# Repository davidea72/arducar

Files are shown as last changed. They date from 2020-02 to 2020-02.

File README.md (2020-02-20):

# arducar
arduino based car with mpu 6050 gyro

l' intento è quello di realizzare una macchinina comandata da un app sul telefono android 

 la macchinina deve andare avanti e indietro , destra e sinistra , deve fermarsi in automatico dopo un po che non riceve comandi 
 
 siccome non si trovano due motori che girino alla stessa velocità la macchinina tende sempre a sterzare da un lato, per correggere questo comportamento si è inserito il giroscopio GY-521 basato sull' mpu 6050
 
 il giroscopio puo' esser utilizzato in modalità normale , o con l' ausilio della DMP interna , in tal caso  va utilizzato il pin dell' interrupt per segnalare ad arduino quando la dmp ha finito i calcoli e i dati sono pronti da leggere 
 
 Anche in tale configurazione ho riscontrato che i primi 20 secondi circa la lettura non è stabile , quindi bisogna aspettare circa 20 secondi affinchè la lettura si stabilizzi (con un errore inferiore a 0.05 gradi) 
 
 ogni volta che la macchinina si ferma viene calcolato un nuovo offset in modo da considerare sempre come rotta 0 gradi la direzione che ha qualche istante prima della partenza 
 
 Per far andare dritta la macchinina quindi , viene passato al PID la rotta attuale , quella voluta (come setpoint) e se ne ottiene il valore da passare ai motori come correzione (output), questo valore è calcolato in base ai 3 parametri Kp , Ki e Kd 
 
 infine viene effettuata una lettura della batteria , tale tensione è ricavata tramite un partitore resistivo da quella di alimentazione dai supercondensatori , la lettura è riparametrizzata tra due valori che corrispondono a 7V - 0% e 11,7V 100% 
 l' app sul telefonino è stata creata tramite appinventor , del quale ho apprezzato la facilità d' uso ma ho anche trovato uno dei suoi limiti , non è possibile processare un grosso flusso dati dalla macchinina verso il telefonino , se mando tutti i dati di debug  sull' app vanno accumulando ritardo, arrivando ad una decina di secondi di ritardo fino a bloccare a volte l' app 
 
 Per debuggare sono stato costretto ad utilizzare il portatile collegato in bluetooth alla macchinina con un emulatore terminale quale minicom. 
 per facilitare il debug , le varie parti di debug sono attivabili e disattivabili a runtime , cosi' come anche i parametri K del pid sono modificabili a runtime con step di 0.5 

 Il file Giulia.aia è il progetto da importare su app inventor per creare e/o modificare l' app android creata da Giulia

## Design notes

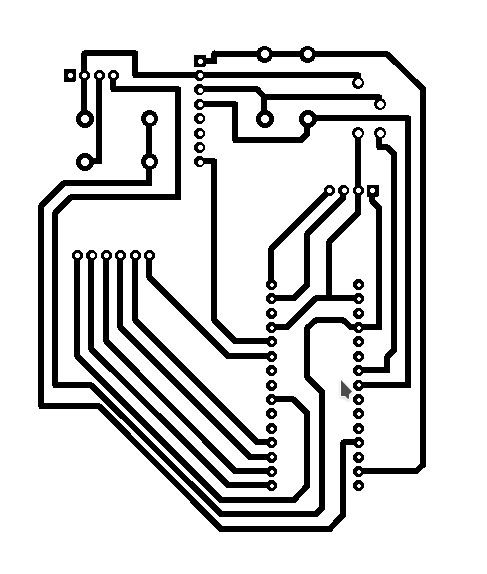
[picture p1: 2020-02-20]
stampato_rame.png

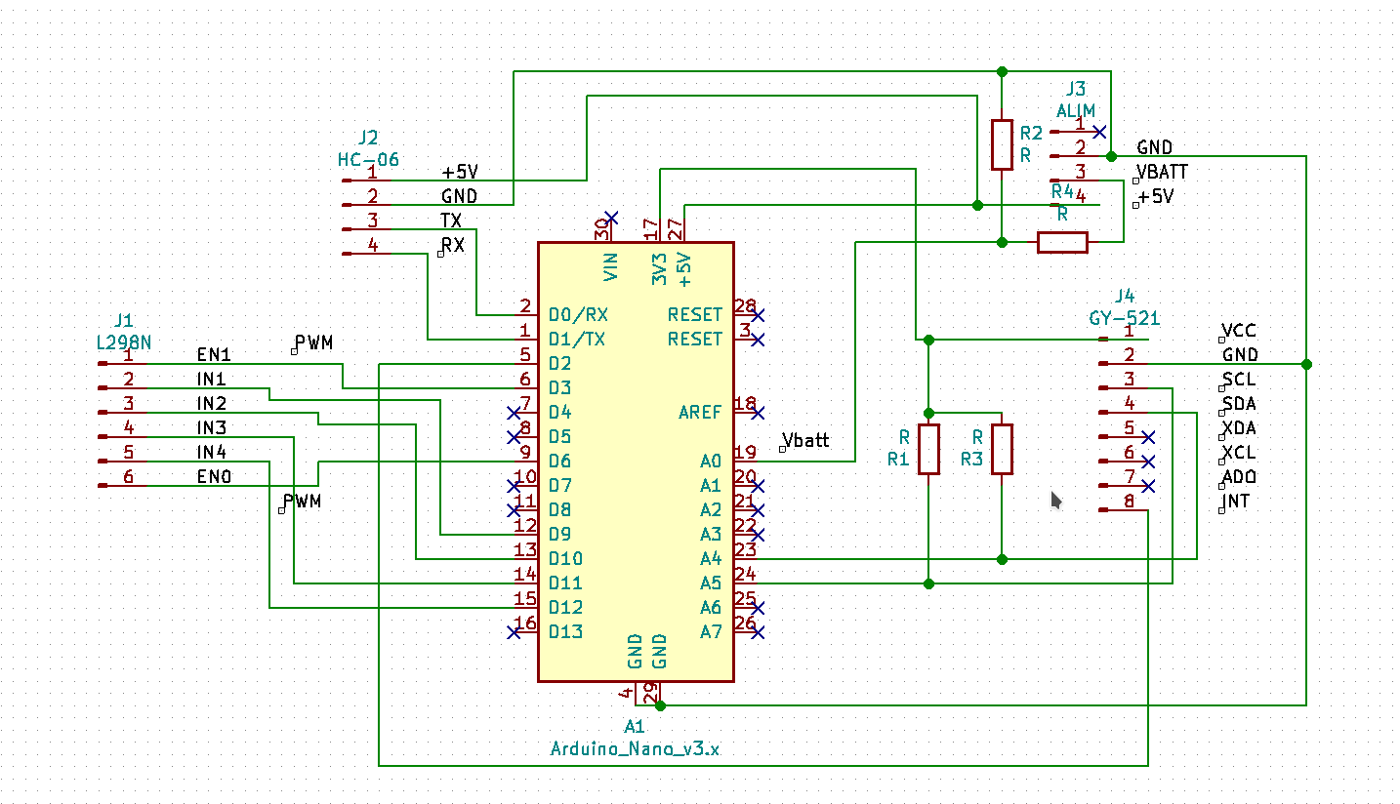
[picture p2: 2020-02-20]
schema_elettrico.png

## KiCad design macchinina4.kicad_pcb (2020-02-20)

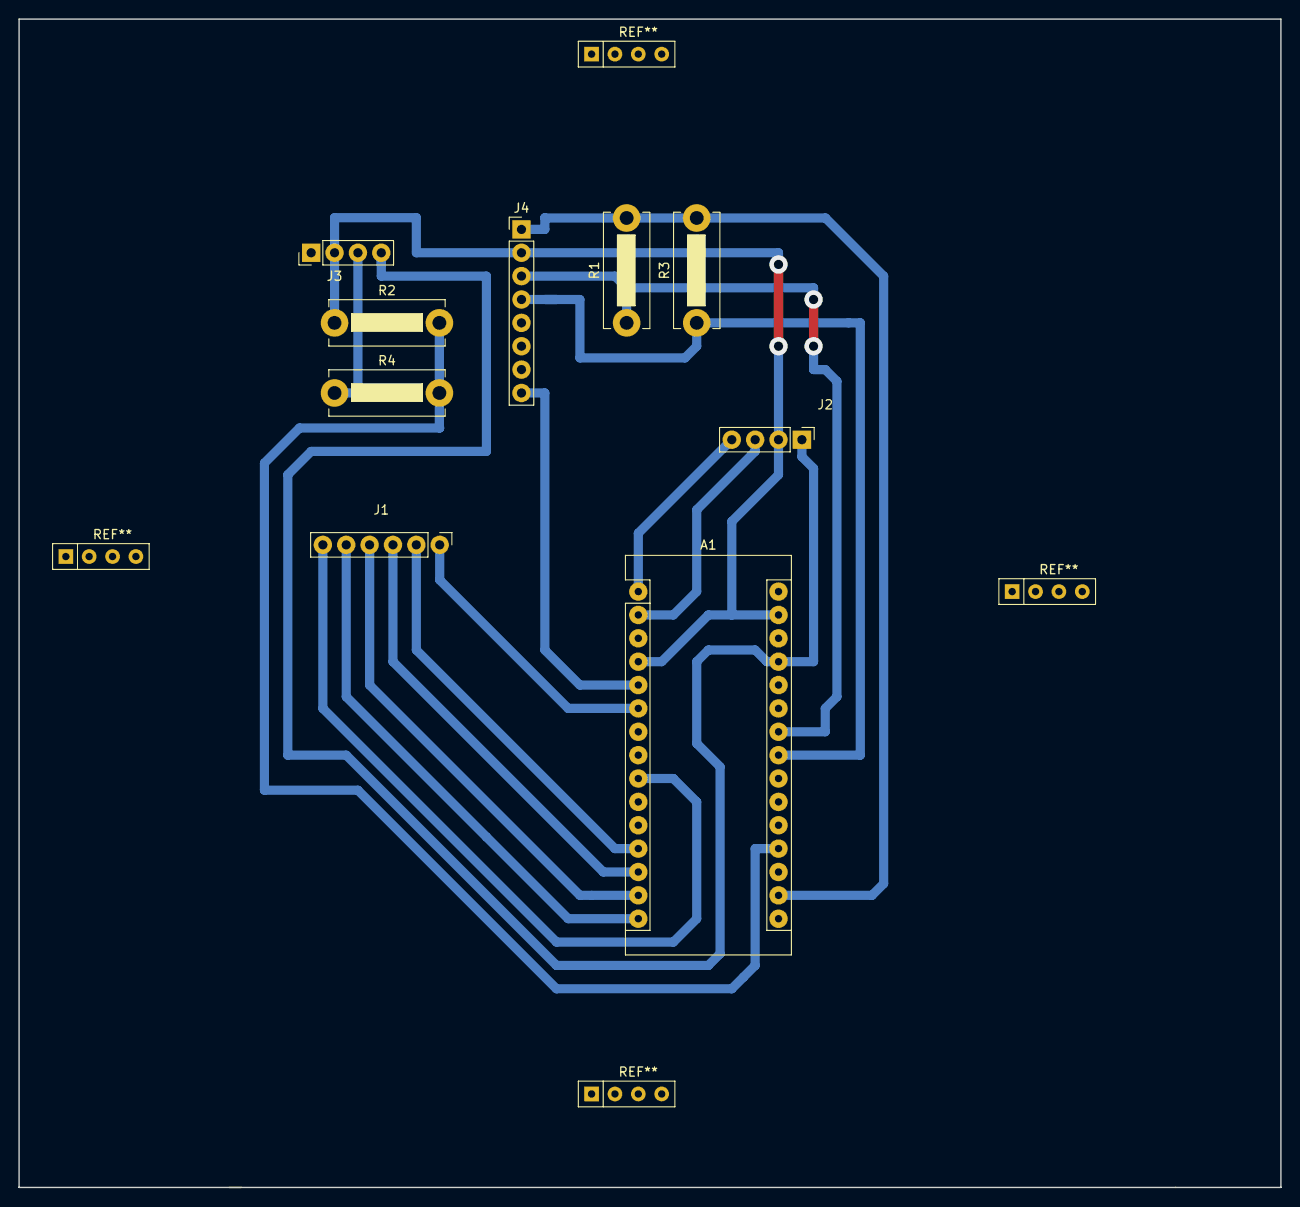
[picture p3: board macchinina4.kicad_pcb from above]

Board: 2 copper layers, 137.2 x 127.0 mm, 9 parts (0 on the bottom side), 16 nets.

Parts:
A1: Arduino_Nano_v3.x; Arduino_Nano
J1: L298N; PinHeader_1x06_P2.54mm_Vertical
J2: HC-06; PinHeader_1x04_P2.54mm_Vertical
J3: ALIM; PinHeader_1x04_P2.54mm_Vertical
J4: GY-521; PinHeader_1x08_P2.54mm_Vertical
R1, R2, R3, R4: R; R_Bare_Metal_Element_L12.4mm_W4.8mm_P11.40mm

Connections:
/+5V: A1.27, J2.1, J3.4
/EN0: A1.9, J1.6
/EN1: A1.6, J1.1
/GND: A1.4, A1.29, J2.2, J3.2, J4.2, R2.1
/IN1: A1.12, J1.2
/IN2: A1.13, J1.3
/IN3: A1.14, J1.4
/IN4: A1.15, J1.5
/TX: A1.2, J2.3
unnamed: A1.1, J2.4
unnamed: A1.5, J4.8
unnamed: A1.17, J4.1, R1.2, R3.2
unnamed: A1.19, R2.2, R4.2
unnamed: A1.23, J4.4, R3.1
unnamed: A1.24, J4.3, R1.1
unnamed: J3.3, R4.1

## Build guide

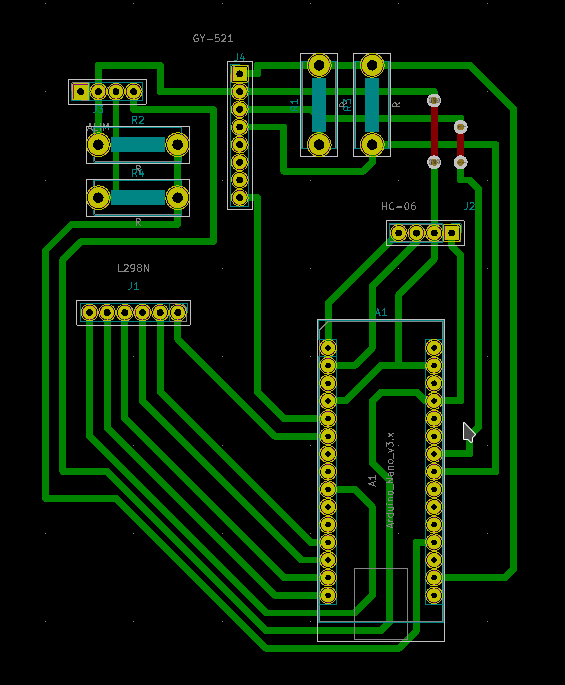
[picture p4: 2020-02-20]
stampato_montaggio.png

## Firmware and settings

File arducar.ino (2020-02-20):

/*
 * l' intento è quello di realizzare una macchinina comandata da un app sul telefono android
 * la macchinina deve andare avanti e indietro , destra e sinistra , deve fermarsi in automatico dopo un po che non riceve comandi
 * siccome non si trovano due motori che girino alla stessa velocità la macchinina tende sempre a sterzare da un lato
 * per correggere questo comportamento si è inserito il giroscopio GY-521 basato sull' mpu 6050
 * il giroscopio puo' esser utilizzato in modalità normale , o con l' ausilio della DMP interna , in tal caso
 * va utilizzato il pin dell' interrupt per segnalare ad arduino quando la dmp ha finito i calcoli e i dati sono pronti da leggere
 * anche in tale configurazione ho riscontrato che i primi 20 secondi circa la lettura non è stabile , quindi bisogna aspettare
 * circa 20 secondi affinchè la lettura si stabilizzi (con un errore inferiore a 0.05 gradi)
 * quindi ogni volta che la macchinina si ferma viene calcolato un nuovo offset in modo da calcolare sempre come rotta 0 gradi la direzione  
 * qualche istante prima della partenza
 * per far andare dritta la macchinina quindi , viene passato al PID la rotta attuale , quella voluta (come setpoit) e se ne ottiene il valore 
 * da passare ai motori come correzione (output)  , questo valore è calcolato in base ai 3 parametri Kp , Ki e Kd
 * infine viene effettuata una lettura della batteria , tale tensione è ricavata tramite un partitore resistivo da quella di alimentazione dai
 * supercondensatori , la lettura è riparametrizzata tra due valori che corrispondono a 7V - 0% e 11,7V 100%
 * 
 * l' app sul telefonino è stata creata tramite appinventor , del quale ho apprezzato la facilità d' uso ma ho anche trovato uno dei suoi 
 * limiti , non è possibile processare un grosso flusso dati dalla macchinina verso il telefonino , se mando tutti i dati di debug
 * sull' app vanno accumulando ritardo, arrivando ad una decina di secondi di ritardo fino a bloccare a volte l' app
 * 
 * quindi per debuggare sono stato costretto ad utilizzare il portatile collegato in bluetoot alla macchinina con un emulatore terminale
 * quale minicom.
 * per facilitare il debug , le varie parti di debug sono attivabili e disattivabili a runtime , cosi' come anche i parametri K del pid sono
 * modificabili a runtime con step di 0.5
 * 
 * 
 */

bool debug_cmd = false;
bool debug_imbardata = false;
bool debug_batt = false;
bool debug_pwm = false;
bool debug_pid = false;
bool report_batteria = true;
#define direzione_motoreSXA  11 // D11
#define direzione_motoreSXB  12 // D12
#define direzione_motoreDXA  9 //D9
#define direzione_motoreDXB  10 //D10
#define pwm_motor_SX  6 //PWM D6// A4 SDA
#define pwm_motor_DX  3 //PWM D3
#define battery 0 // A0
#define UP  'U'         //comando per andare avanti o aumentare la velocita in avanti/ridurre quella in indietro
#define DOWN  'D'       //comando per andare indietro o aumentare la velocita indietro/ridurre quella in avanti
#define LEFT 'L'
#define RIGHT 'R'
#define debug_cmd_on 'a'
#define debug_cmd_off 'b'
#define debug_imbardata_on 'c'
#define debug_imbardata_off 'd'
#define debug_batt_on 'e'
#define debug_batt_off 'f'
#define debug_pwm_on 'g'
#define debug_pwm_off 'h'
#define debug_pid_on 'i'
#define debug_pid_off 'l'
#define report_batteria_on 'm'
#define report_batteria_off 'n'
#define Kp_add 'o'
#define Kp_sub 'p'
#define Ki_add 'q'
#define Ki_sub 'r'
#define Kd_add 's'
#define Kd_sub 't'

#include "I2Cdev.h"
#include "MPU6050_6Axis_MotionApps20.h"
#include <PID_v1.h>
#include "motore.h"

#if I2CDEV_IMPLEMENTATION == I2CDEV_ARDUINO_WIRE
#include "Wire.h"
#endif


MPU6050 mpu;

//variabili necessarie alla lettura del giroscopio

bool dmpReady = false;  // set true if DMP init was successful
uint8_t mpuIntStatus;   // holds actual interrupt status byte from MPU
uint8_t devStatus;      // return status after each device operation (0 = success, !0 = error)
uint16_t packetSize;    // expected DMP packet size (default is 42 bytes)
uint16_t fifoCount;     // count of all bytes currently in FIFO
uint8_t fifoBuffer[64]; // FIFO storage buffer
Quaternion q;           // [w, x, y, z]         quaternion container
VectorFloat gravity;    // [x, y, z]            gravity vector
float ypr[3];           // [yaw, pitch, roll]   yaw/pitch/roll container and gravity vector
float offsetX, offsetY, offsetZ;


//variabili necessarie al controllo PID
double Setpoint = 0, Output, imbardata = 0, imbardata_gradi, imbardata_netta, rotta;
double Kp = 3;
double Ki = 1.1;
double Kd = 20;


PID myPID(&rotta, &Output, &Setpoint, Kp, Ki, Kd, P_ON_E, DIRECT); 
/*
 * 
 *  P_ON_M specifies that Proportional on Measurement be used
 *  P_ON_E (Proportional on Error) is the default behavior 
 *  
 *  rotta: The variable we're trying to control (double)
 *  Output: The variable that will be adjusted by the pid (double) 
 *  Setpoint: The value we want to Input to maintain (double)
 *  
 *  Kp, Ki, Kd: Tuning Parameters. these affect how the pid will change the output. (double>=0)
 *  Direction: Either DIRECT or REVERSE. determines which direction the output will move when faced with a given error. DIRECT is most common.
 *  Kp: Determines how aggressively the PID reacts to the current amount of error (Proportional) (double >=0)
 *  Ki: Determines how aggressively the PID reacts to error over time (Integral) (double>=0)
 *  Kd: Determines how aggressively the PID reacts to the change in error (Derivative) (double>=0)
 *  
 */




// ================================================================
// ===               INTERRUPT DETECTION ROUTINE                ===
// ================================================================

volatile bool mpuInterrupt = false;     // indicates whether MPU interrupt pin has gone high
void dmpDataReady() {
  mpuInterrupt = true;
  //Serial.println("interrupt");

}

/*
 * 
 * lo schetch definisce i pin in testa direttamente come define
 * vengono utilizzati i seguenti pin 
 * direzione_motoreSXA  11 // D11
 * direzione_motoreSXB  12 // D12
 * direzione_motoreDXA  9 //D9
 * direzione_motoreDXB  10 //D10
 * pwm_motor_SX  6 //PWM D6// A4 SDA
 * pwm_motor_DX  3 //PWM D3
 * battery 0 // A0
 * 
 * tale sequenza è stata scelta cosi' anche in funzione del circuito stampato che ho realizzato
 * inoltre vengono utilizzati i pin
 * A5 SCL 
 * A4 SDL
 * per il dialoco I2C con giroscopio
 * 
 */


//definizione variabili

int sterzata = 0;
char received = "";     // variabile per ricezione da bluetooth
int potenza = 0;
int tensione;
char tensione_percentuale[2];
int every = 0;        //variabile usata per contare ogni quanti cicli mandare fuori dei dati , viene calcolato il modulo % in base a quanto volgiamo sia veloce
bool calibrated = false;  //utilizzata per bloccare il funzionamento della macchinina finche il giroscopio non si stabilizza
int cal_count = 500;      //quanti cicli dobbiamo aspettare prima di considerare stabilizzato il giroscopio
int cicle_from_start= 0;  //cicli (loop) dall' avvio
int ritardo = 30;         //tempo di attesa a fine loop
int flash_every = 30;     //ogni quanti cicli deve flashare il led
double milli, old_milli, tot_milli;   //variabili utilizzate per il debug



// ================================================================
// ===                      INITIAL SETUP                       ===
// ================================================================

void setup() {
  pinMode(LED_BUILTIN, OUTPUT);
  pinMode(direzione_motoreSXA, OUTPUT);
  pinMode(direzione_motoreSXB, OUTPUT);
  pinMode(pwm_motor_SX, OUTPUT);
  pinMode(direzione_motoreDXA, OUTPUT);
  pinMode(direzione_motoreDXB, OUTPUT);
  pinMode(pwm_motor_DX, OUTPUT);
  Serial.begin(115200);
  // join I2C bus (I2Cdev library doesn't do this automatically)
#if I2CDEV_IMPLEMENTATION == I2CDEV_ARDUINO_WIRE
  Wire.begin();
  TWBR = 24; // 400kHz I2C clock (200kHz if CPU is 8MHz)
#elif I2CDEV_IMPLEMENTATION == I2CDEV_BUILTIN_FASTWIRE
  Fastwire::setup(400, true);
#endif

  // initialize device
  mpu.initialize();


  // load and configure the DMP
  devStatus = mpu.dmpInitialize();

  // supply your own gyro offsets here, scaled for min sensitivity
  mpu.setXGyroOffset(0);
  mpu.setYGyroOffset(0);
  mpu.setZGyroOffset(0);
  mpu.setZAccelOffset(0); // 1688 factory default for my test chip


  // make sure it worked (returns 0 if so)
  if (devStatus == 0) {
    // turn on the DMP, now that it's ready
    mpu.setDMPEnabled(true);

    // enable Arduino interrupt detection
    attachInterrupt(0, dmpDataReady, RISING);
    mpuIntStatus = mpu.getIntStatus();

    // set our DMP Ready flag so the main loop() function knows it's okay to use it
    dmpReady = true;

    // get expected DMP packet size for later comparison
    packetSize = mpu.dmpGetFIFOPacketSize();
  }
  myPID.SetOutputLimits(-90, 90);
  myPID.SetSampleTime(20);
  myPID.SetMode(AUTOMATIC);

}



// ================================================================
// ===                    MAIN PROGRAM LOOP                     ===
// ================================================================

void loop() {

  // if programming failed, don't try to do anything
  if (!dmpReady) return;

  // wait for MPU interrupt or extra packet(s) available
  while (!mpuInterrupt && fifoCount < packetSize) {



  }


  if (Serial.available() > 0 )
  {
    received = Serial.read();
    //Serial.println(received);

  }



  //il comando di potenza non puo' eccedere il valore di 120 per lasciare spazio alla correzione

  switch (received) {
    case  UP:
      if ( potenza < 120) {
        potenza += 10;
        Serial.flush();
        if (debug_cmd) {

        }

      }
      break;

    case DOWN:
      if ( potenza > -120) {
        potenza -= 10;
        Serial.flush();
        if (debug_cmd) {
        }
        Serial.flush();
      }
      break;

    case LEFT:
      sterzata += 10;
      Serial.flush();
      break;
      
    case RIGHT:
      sterzata -= 5;
      Serial.flush();
      break;

    case debug_cmd_on:
      debug_cmd = true;
      Serial.println("debug comandi avviato");
      break;

    case debug_cmd_off:
      debug_cmd = false;
      Serial.println("debug comandi fermato");
      break;


    case debug_imbardata_on:
      debug_imbardata = true;
      Serial.println("debug imbardata avviato");
      break;

    case debug_imbardata_off:
      debug_imbardata = false;
      Serial.println("debug imbardata fermato");
      break;


    case debug_batt_on:
      debug_batt = true;
      Serial.println("debug batteria avviato");
      break;

    case debug_batt_off:
      debug_batt = false;
      Serial.println("debug batteria fermato");
      break;


    case debug_pwm_on:
      debug_pwm = true;
      Serial.println("debug pwm avviato");
      break;

    case debug_pwm_off:
      debug_pwm = false;
      Serial.println("debug pwm fermato");
      break;


    case debug_pid_on:
      debug_pid = true;
      Serial.println("debug pid avviato");
      break;

    case debug_pid_off:
      debug_pid = false;
      Serial.println("debug pid fermato");
      break;

    case report_batteria_on:
      report_batteria = true;
      Serial.println("report batteria avviato");
      break;

    case report_batteria_off:
      report_batteria = false;
      Serial.println("report batteria fermato");
      break;

    case Kp_add:
      Kp += 0.5;
      myPID.SetTunings(Kp, Ki, Kd);
      break;

    case Kp_sub:
      Kp -= 0.5;
      myPID.SetTunings(Kp, Ki, Kd);
      break;

    case Ki_add:
      Ki += 0.5;
      myPID.SetTunings(Kp, Ki, Kd);
      break;

    case Ki_sub:
      Ki -= 0.5;
      myPID.SetTunings(Kp, Ki, Kd);
      break;

    case Kd_add:
      Kd += 0.5;
      myPID.SetTunings(Kp, Ki, Kd);
      break;

    case Kd_sub:
      Kd -= 0.5;
      myPID.SetTunings(Kp, Ki, Kd);
      break;

    default:
      Serial.flush();

  }


  every += 1;
  if (potenza > 0 and every % 10 == 0) {
    potenza -= 1;
    every = 0;
  }

  if (potenza < 0 and every % 10 == 0) {
    potenza += 1;
    every = 0;
  }

  if (calibrated == true and potenza != 0) {
    myPID.Compute();
    if (debug_pid) {
      milli = millis();
      Serial.print("D:");
      Serial.print(milli - old_milli);

      old_milli = milli;
      tot_milli += old_milli;
      Serial.print(" ");
      Serial.print(old_milli);
      Serial.print("\tKp,Ki,Kd = ");
      Serial.print(Kp);
      Serial.print(",");
      Serial.print(Ki);
      Serial.print(",");
      Serial.print(Kd);
      Serial.print("\timbardata= ");
      Serial.print(imbardata);
      Serial.print("\tsterzata = ");
      Serial.print(sterzata);
      Serial.print("\t rotta= ");
      Serial.print(rotta);
      Serial.print(" valore output= ");
      Serial.println(Output);

    } else {
      tot_milli = 0;
    }

  }

  if (debug_imbardata and potenza != 0) {
    Serial.print("D:");
    Serial.print("imbardata_gradi = ");
    Serial.print(imbardata_gradi);
    Serial.print(" imbardata_netta = ");
    Serial.print(imbardata_netta);

    Serial.print("imbardata = ");
    Serial.print(imbardata);
    Serial.print(" output = ");
    Serial.println(Output);
  }

    if (calibrated == true) {
    driver_motore(&potenza, &Output);
  }

  if (every % 5 == 0) {


    lettura_batteria();
  }


  delay(ritardo);





  // reset interrupt flag and get INT_STATUS byte
  mpuInterrupt = false;
  mpuIntStatus = mpu.getIntStatus();

  // get current FIFO count
  fifoCount = mpu.getFIFOCount();

  // check for overflow (this should never happen unless our code is too inefficient)
  if ((mpuIntStatus & 0x10) || fifoCount == 1024) {
    // reset so we can continue cleanly
    mpu.resetFIFO();

    // otherwise, check for DMP data ready interrupt (this should happen frequently)
  } else if (mpuIntStatus & 0x02) {
    // wait for correct available data length, should be a VERY short wait

    while (fifoCount < packetSize) fifoCount = mpu.getFIFOCount();

    // read a packet from FIFO
    mpu.getFIFOBytes(fifoBuffer, packetSize);

    // track FIFO count here in case there is > 1 packet available
    // (this lets us immediately read more without waiting for an interrupt)
    fifoCount -= packetSize;


    // display Euler angles in degrees
    mpu.dmpGetQuaternion(&q, fifoBuffer);
    mpu.dmpGetGravity(&gravity, &q);
    mpu.dmpGetYawPitchRoll(ypr, &q, &gravity);

    if (cicle_from_start < cal_count) {
      cicle_from_start++;
      if (cicle_from_start % flash_every == 0) {
        digitalWrite(LED_BUILTIN, !digitalRead(LED_BUILTIN));
      }
    }

    if (calibrated == true && potenza == 0) {
      offsetX = (ypr[0] * 180 / M_PI);
      sterzata = 0;

    }


    if (calibrated == true) {
      imbardata_gradi = ypr[0];
      imbardata_netta = (imbardata_gradi * 180 / M_PI);
      imbardata = ( (int)(imbardata_netta - offsetX)  % 360);
      rotta = imbardata + sterzata;
    }

    if (cicle_from_start == cal_count) {
      offsetX = (ypr[0] * 180 / M_PI);
      offsetY = (ypr[1] * 180 / M_PI);
      offsetZ = (ypr[2] * 180 / M_PI);
      cicle_from_start++;
      digitalWrite(LED_BUILTIN, HIGH);
      calibrated = true;
    }

  }
}







void lettura_batteria () {
  tensione = analogRead(battery);

  if (debug_batt) {
    Serial.print("D:");
    Serial.print("tensione letta ");
    Serial.println(tensione);
  }
  tensione = map(tensione, 480, 750, 0, 100);
  tensione = constrain(tensione, 0, 100);
  itoa(tensione, tensione_percentuale, 10);


  if (report_batteria) {
    Serial.print("B:");
    Serial.println(tensione_percentuale);
  }
}

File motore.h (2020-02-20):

//per Definire il senso di marcia del motore
/*    direzione_motoreA |   direzione_motoreB  | Evento
    --------------------|----------------------|----------------------
           LOW          |        LOW           | fermo
           LOW          |        HIGH          | Movimento in un senso
           HIGH         |        LOW           | Movimento senso opposto
           HIGH         |        HIGH          | Fermo                     */


void driver_motore(int * pot, double * Out) {
int  potenza=*pot;
int correzione=*Out;
int pwmSX = 0;         //  power rimappato in scala da 0 a 255 per l' output
int pwmDX = 0;         //  power rimappato in scala da 0 a 255 per l' output
int powerSX = 0;        // potenza generale pwmSX
int powerDX = 0;        // potenza generale pwmDX

/*
 * 
 * gira piu' veloce il motore destro
 * 
 * 
 */
  if (potenza == 0) {
    
    
    digitalWrite(direzione_motoreSXA, LOW);
    digitalWrite(direzione_motoreSXB, LOW);
    digitalWrite(direzione_motoreDXA, LOW);
    digitalWrite(direzione_motoreDXB, LOW);
    pwmSX=0;
    pwmDX=0;
    powerSX=0;
    powerDX=0;
    
  }
  else if (potenza > 0) {
    
    if (debug_pwm) {
      Serial.print("D:");
    Serial.print("avanti ");
    Serial.println(correzione);
    }
    
    digitalWrite(direzione_motoreSXA, LOW);
    digitalWrite(direzione_motoreSXB, HIGH);
    digitalWrite(direzione_motoreDXA, LOW);
    digitalWrite(direzione_motoreDXB, HIGH);

    powerSX=potenza+correzione;
    
    powerDX=potenza;
    
    
    powerSX=constrain(powerSX,0,255);
    powerDX=constrain(powerDX,0,255);
    //map(value, fromLow, fromHigh, toLow, toHigh)
    pwmSX = map(powerSX, 0, 255, 80, 255);
    pwmDX = map(powerDX, 0, 255, 80, 255);
    
  }
  else {
    analogWrite(pwm_motor_SX, pwmSX);
    analogWrite(pwm_motor_DX, pwmDX);

    if (debug_pwm) {
      Serial.print("D:");
    Serial.print("indietro ");
    }
    
    digitalWrite(direzione_motoreSXA, HIGH);
    digitalWrite(direzione_motoreSXB, LOW);
    digitalWrite(direzione_motoreDXA, HIGH);
    digitalWrite(direzione_motoreDXB, LOW);

     powerSX=potenza+correzione;
     
    powerDX=potenza;
    
    powerSX=constrain(powerSX,-255,0);
    powerDX=constrain(powerDX,-255,0);
    
    //map(value, fromLow, fromHigh, toLow, toHigh)
    pwmSX = map(powerSX, -255, 0, 255, 80);
    pwmDX = map(powerDX, -255, 0, 255, 80);
    

  }
  
  if (debug_pwm and potenza !=0) {
    Serial.print("potenza ");
    Serial.print(potenza);
    Serial.print(" correzione ");
    Serial.print(correzione);
    Serial.print(" powerSX ");
    Serial.print(powerSX);
    Serial.print(" powerDX ");
    Serial.print(powerDX);
    Serial.print(" pwm value sx ");
    Serial.print(pwmSX);
    Serial.print(" dx ");
    Serial.println(pwmDX);
  }
  
  analogWrite(pwm_motor_SX, pwmSX);
  analogWrite(pwm_motor_DX, pwmDX);

} 

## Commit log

2020-02-20 schema elettrico kicad
    [macchinina.sch]
2020-02-20 pcb kicad
    [macchinina4.kicad_pcb]
